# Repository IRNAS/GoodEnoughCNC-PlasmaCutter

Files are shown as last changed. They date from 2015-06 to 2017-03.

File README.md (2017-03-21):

# GoodEnoughCNC-Hybrid

#### ! PLEASE NOTE THAT WE NO LONGER ACTIVELY SUPPORT THIS PROJECT. 

**GoodEnoughCNC Hybrid - very low cost and simple, suitable for everyone. Can be mill, plasma or laser cutter.**

You can find out more on the project website - [goodenoughcnc.eu](http://goodenoughcnc.eu/). Step-by-step assembly instructions are available at [instructions.goodenoughcnc.eu](http://instructions.goodenoughcnc.eu/). 

**Technical files for the last, improved version are available in the folder [HybridCNC_v3](https://github.com/IRNAS/GoodEnoughCNC-PlasmaCutter/tree/master/HybridCNC_v3). Please note that these improvements are not included in the [HybridCNC assembly instructions](http://instructions.goodenoughcnc.eu/).**

Industry in vast majority aims to use highest precision and reliability machines, to be capable of producing even the most complicated parts designers come up with. We are flipping such approach on its head, trading precision of manufacturing tools for simplicity and low cost of their construction, to reduce the entry barrier for using them in any environment. 

GoodEnoughCNC-PlasmaCutter

## Prototype Specifications
Every machine can be tailored to size.
The GoodEnoughCNC Hybrid is a parametric bootstrap machine. Dimensions depend on the length of the profiles (Parameter L) and profile sizes. The specification below applies for L=1200mm profiles. 

### Frame Metric
 * 40 mm steel tubes
 * 3 mm thickness

### Trolleys Metric
 * 100 mm steel tubes
 * 3 mm thicknes

### Footprint
 * Width: 1450 mm 
 * Length: 900 mm

### Cutting area
 * Width: L-900 mm
 * Length: L-900 mm

### Z travel
 * Height: Z axis rod length - 150 mm

### XY Motion system
 * Timing belt and pulley (T5 or HTD5M or HTD3M or GT2[worst case])
 * Nema 23 motors

### Z Motion system
 * Threaded rod
 * Nema 17 motor

### Plasma
 * Low cost hand held plasma (BMF CUT 50M) or similar
 * THC (Torch height controller)
 * Compressor 30-100 l/min at 2-4 bar – effective 180 l/min

###CNC Controller
Any 4 channel CNC controller, tested:
 * Planet CNC MK3/4 USB Controller
 * Stepper drivers 2.5 A
 * 24 or 48 VDC Power supply

## Features

### Simplicity
Can be manufactured using a hand held drill and angle grinder. Non critical parts are 3D and can be made using other manufacturing processes

### Frame
Low cost Square tubes are used as structural components and linear rails for trolleys. The frame is kept in rectangular position using two turnbuckles. Removing the turnbuckles allows folding the frame for easy transport. 

GoodEnoughCNC-PlasmaCutter

GoodEnoughCNC-PlasmaCutter

### Trolleys
Low cost square tubes with holes for motor, bearing positions and tightening. Tightening mechanisms compensate for loose tolerances in hole positioning. The result is a exact fit on the frame.

GoodEnoughCNC-PlasmaCutter

GoodEnoughCNC-PlasmaCutter

### Z Axis
Lighter and simpler to manufacture, the Z axis mechanism does not require milled parts like conventional solutions. The torch holder tightly locks the torch in place without having to modify the handle.

GoodEnoughCNC-PlasmaCutter

### Plasma
The Chinese BMF CUT 50M plasma cutter packs more than enough punch to cleanly cut up to 5 mm sheet metal (10 mm max cut). Additionally a compressor and torch height controller is needed.

GoodEnoughCNC-PlasmaCutter

## Control system
A number of different CNC controller systems may be applied to this machine. Additionally we have developed an unique fibre optics based interface for the plasma cutter itself, reducing the cost of adding a Torch Height Controller with our custom design, enabling cutting of warped or corrugated surfaces.

### Configuration for CNC control systems
 * Steps per unit X, Y (steps/mm): 67.67 (using 1/16 microstepping by default)
 * Steps per unit Z (steps/mm): 2560 (using 1/16 microstepping by default)
 * Maximum speed X, Y(mm/min): 8000
 * Maximum speed Z (mm/min): 250
 * Acceleration X,Y (mm^2/min): 80
 * Acceleration Z (mm^2/min): 25
 
Setting file for PlanetCNC is [available](goodenoughcnc-hybrid-planetcnc.setting).

### Configuring Goodrive10 VFD inverter for 0.8kW watercooled spindle
Manufacturers [user manual for Goodrive10](http://www.invt.com/UploadFiles/en/Files/2013/9/Goodrive10%20Operation%20Manual(V1.3).pdf) documents well all the features. Spindle specific settings for 0.8kW spindle are, modified from defaults:
 * P00.03 400
 * P00.04 400
 * P02.02 400
 
With this the spindle should run at 24000rpm, note the display either shows 24000 in rpm or 400 in Hz, both representing the same speed.

## Q&A

[Here](https://github.com/IRNAS/GoodEnoughCNC-PlasmaCutter/blob/master/Q%26A.md) you can read the answers to some frequently asked questions.

---

#### License

All our projects are as usefully open-source as possible.

Hardware including documentation is licensed under [CERN OHL v.1.2. license](http://www.ohwr.org/licenses/cern-ohl/v1.2)

Firmware and software originating from the project is licensed under [GNU GENERAL PUBLIC LICENSE v3](http://www.gnu.org/licenses/gpl-3.0.en.html).

Open data generated by our projects is licensed under [CC0](https://creativecommons.org/publicdomain/zero/1.0/legalcode).

All our websites and additional documentation are licensed under [Creative Commons Attribution-ShareAlike 4 .0 Unported License] (https://creativecommons.org/licenses/by-sa/4.0/legalcode).

What this means is that you can use hardware, firmware, software and documentation without paying a royalty and knowing that you'll be able to use your version forever. You are also free to make changes but if you share these changes then you have to do so on the same conditions that you enjoy.

Koruza, GoodEnoughCNC and IRNAS are all names and marks of Institut IRNAS Rače. 
You may use these names and terms only to attribute the appropriate entity as required by the Open Licences referred to above. You may not use them in any other way and in particular you may not use them to imply endorsement or authorization of any hardware that you design, make or sell.

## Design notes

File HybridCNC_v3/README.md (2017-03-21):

# HybridCNC Improvements

Here you can find documentation for several improvements to our GoodEnoughCNC Hybrid, which are simplifying the design and making the machine more robust. Everyone interested only in the changes compared to previous version can find the changed files in the folder [HybridCNC-Changed-files-only](https://github.com/IRNAS/GoodEnoughCNC-PlasmaCutter/tree/master/HybridCNC_v3/HybridCNC-Changed-files-only). Please note that these improvements are not included in the [HybridCNC assembly instructions](https://goodenoughcnc-hybrid-cnc.readme.io/docs). 

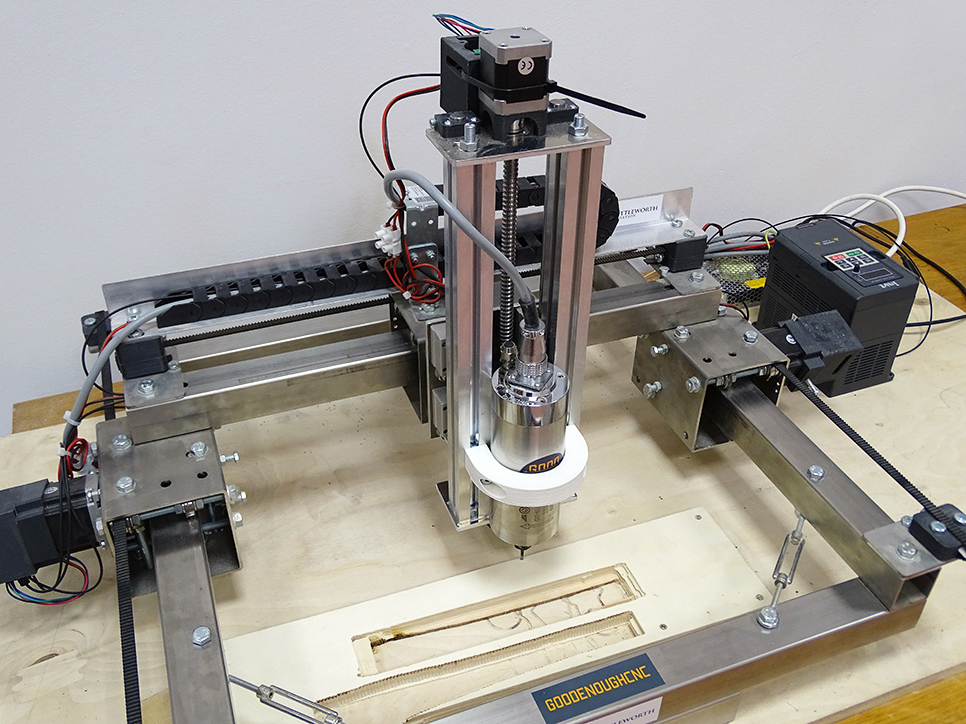
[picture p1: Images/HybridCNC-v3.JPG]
HybridCNC-v3


## Z axis

We completely changed the structure of the Z axis. Instead of the axial bearings used for railing system we decided to use a linear bearing with casings, which makes the axis sturdier and much more accurate. We replaced the M8 rod used for linear movement of the Z axis with a ball screw and an anti backlash nut with 4 mm pitch, further increasing the accuracy of the whole system, enabling finer movement and longer lifetime. The base plate is now made out of 5 mm aluminium plate, which also increases the structural strength. 

HybridCNC-z-axis

## Tightener

We made some minor changes to the tighteners, mostly reducing parts count and enabling easier installation. The tightener bracket is now a one piece laser cut part made out of tubular stainless steel profile. We also replaced the nuts with a screwing tightener with threads already implemented into the model.

HybridCNC-tightener

## Beam short for trolley assembly

We added inspection holes used in mounting process of the ball bearings, which help with accurate placement of the ball bearings.

HybridCNC-trolley

---

#### License

All our projects are as usefully open-source as possible.

Hardware including documentation is licensed under [CERN OHL v.1.2. license](http://www.ohwr.org/licenses/cern-ohl/v1.2)

Firmware and software originating from the project is licensed under [GNU GENERAL PUBLIC LICENSE v3](http://www.gnu.org/licenses/gpl-3.0.en.html).

Open data generated by our projects is licensed under [CC0](https://creativecommons.org/publicdomain/zero/1.0/legalcode).

All our websites and additional documentation are licensed under [Creative Commons Attribution-ShareAlike 4 .0 Unported License] (https://creativecommons.org/licenses/by-sa/4.0/legalcode).

What this means is that you can use hardware, firmware, software and documentation without paying a royalty and knowing that you'll be able to use your version forever. You are also free to make changes but if you share these changes then you have to do so on the same conditions that you enjoy.

Koruza, GoodEnoughCNC and IRNAS are all names and marks of Institut IRNAS Rače. 
You may use these names and terms only to attribute the appropriate entity as required by the Open Licences referred to above. You may not use them in any other way and in particular you may not use them to imply endorsement or authorization of any hardware that you design, make or sell.

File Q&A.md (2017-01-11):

#GoodEnoughCNC Q&A

Here you can read the answers to some frequently asked questions. Please get in touch via [chat](https://chat.irnas.eu/home), [forum](https://goodenoughcnc-hybrid-cnc.readme.io/discuss) or [email](mailto:info@irnas.eu) if you don't find what you're looking for below.

**1. What are the dimensions of GoodEnoughCNC?**

The default version of GoodeenoughCNC machine is 1.1 m x 1.1 m . We do not recommend exceeding the 2 m x 1.2 m dimensions for plasma operations. For milling it depends on your speed and precision requirements.

**2. Is the machining toolhead included in your GoodEnoughCNC kit?**

GoodEnoughCNC kit is the machine without the toolhead, you can mount a
number of different ones on it:

1) Mill : mechanical subtraction of material with a milling bit suitable for most materials ([0.8 kW watercooled spindle](http://fabrikor.eu/goodenoughcnc-hybrid/toolhead-milling-0.8-kw-spindle) available from our store).

2) Plasma: cutting metal with a conductive arc ([plasma cutting torch](http://fabrikor.eu/goodenoughcnc-hybrid/toolhead-plasma-cutting-41) available from our store).

3) Laser: cutting various materials, subject to laser power. We have no laser cutters in our offer at the moment.

**3. Can I cut or engrave MDF with the laser or plasma? The thickest MDF is 18 mm, can your laser cut it at thoroughly in single pass at that depth?**

MDF you can cut only with a mill, laser cutting it may produce hazardous vapors. You can buy a number of different milling bits for different applications. The spindle we offer uses ER11 collets, meaning it can fit bits with shaft ranging from 1-7 mm.

**4. Can I use my own plasma cutter with GoodEnoughCNC?**

To use any plasma cutter with GoodenoughCNC machine one must 3D print a suitable torch mount, modify the plasma cutter such that cutting can be triggered from the control circuit (for example with GoodenoughCNC optical relay, to be released shortly) and optionally connect a Torch Height Controller unit to the plasma torch.

**5. What software is required to work with GoodEnoughCNC?**

The design and G-code generation is best done with [Autodesk Fusion 360](http://www.autodesk.com/products/fusion-360/overview), free and powerful. You also generally require a PC to run CNC software, you can either choose [Planet-CNC controller](http://fabrikor.eu/goodenoughcnc-hybrid/planet-cnc-usb-controller-mk3-4-4axis) that will be bundled with next generation of GoodenoughCNC Hybrid or use any open-source solution, like Arduino+GRBL and control it with one of many applications that exist, but neither really works that great. [GRBL-panel](https://github.com/gerritv/Grbl-Panel/wiki) seems to be one of the more working ones.

**6. What are configuration settings for CNC Control system?**

A number of different CNC controller systems may be applied to this machine. Additionally we have developed an unique fibre optics based interface for the plasma cutter itself, reducing the cost of adding a Torch Height Controller with our custom design, enabling cutting of warped or corrugated surfaces.

Configuration for CNC control systems
- Steps per unit X, Y (steps/mm): 67.67 (using 1/16 microstepping by default)
- Steps per unit Z (steps/mm): 2560 (using 1/16 microstepping by default)
- Maximum speed X, Y(mm/min): 8000
- Maximum speed Z (mm/min): 250
- Acceleration X,Y (mm^2/min): 80
- Acceleration Z (mm^2/min): 25

Setting file for PlanetCNC is available [here](https://github.com/IRNAS/GoodEnoughCNC-PlasmaCutter/blob/master/goodenoughcnc-hybrid-planetcnc.setting).

**7. We cannot configure the inverter for spindle. Do you have a manual or something so that we can change the rpm of the spindle?**

Configuring Goodrive10 VFD inverter for 0.8 kW watercooled spindle:

[Manufacturers user manual](www.invt.com/UploadFiles/en/Files/2013/9/Goodrive10%20Operation%20Manual(V1.3).pdf) for Goodrive10 documents well all the features. Spindle specific settings for 0.8kW spindle are, modified from defaults:
- P00.03 400
- P00.04 400
- P02.02 400

With this the spindle should run at 24000 rpm, note the display either shows 24000 in rpm or 400 in Hz, both representing the same speed.

**8. The collet falls from the spindle after some time. What can I do?**

Collet falls from spindle if it is rotating anti-clockwise, please check the rotation direction. You can change the direction by swapping the U and W wires on VFD.

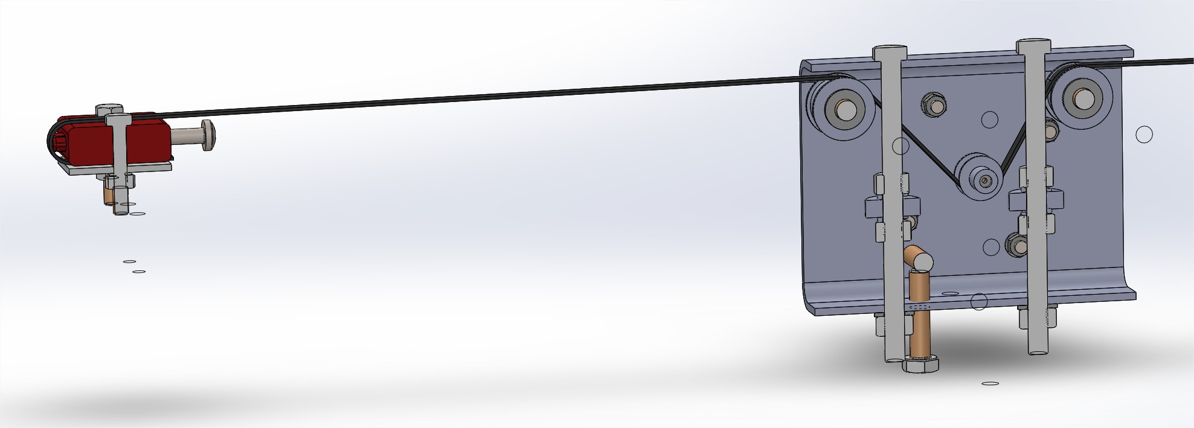
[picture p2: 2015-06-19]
Images/Trolley_inside.jpg

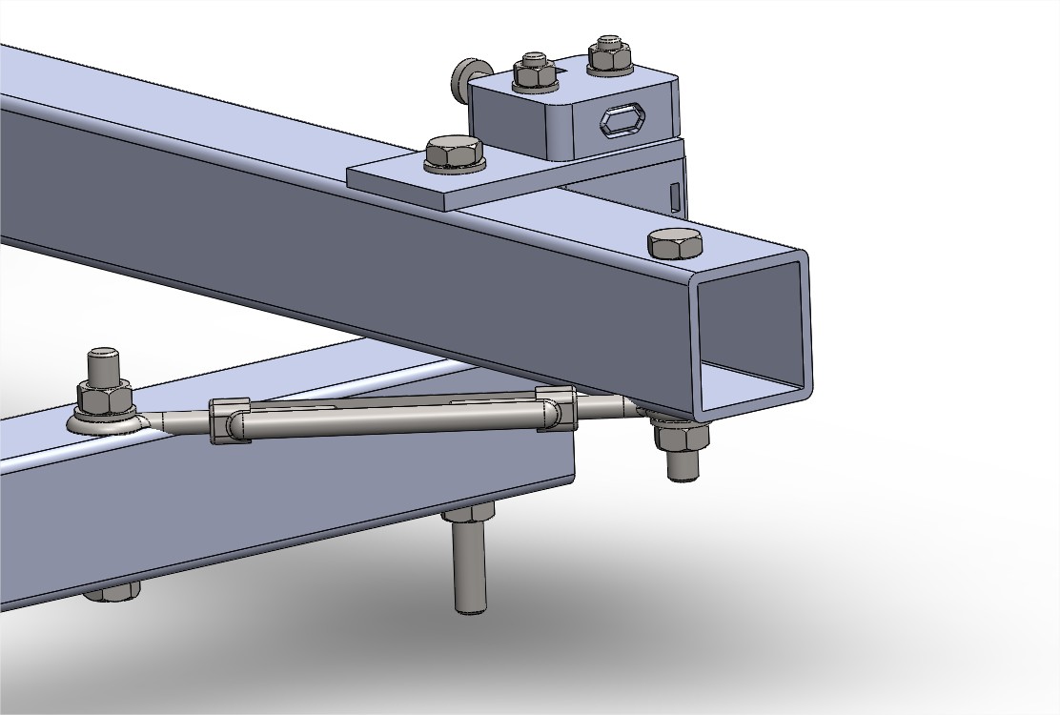
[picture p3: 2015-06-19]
Images/Turnbuckles.jpg

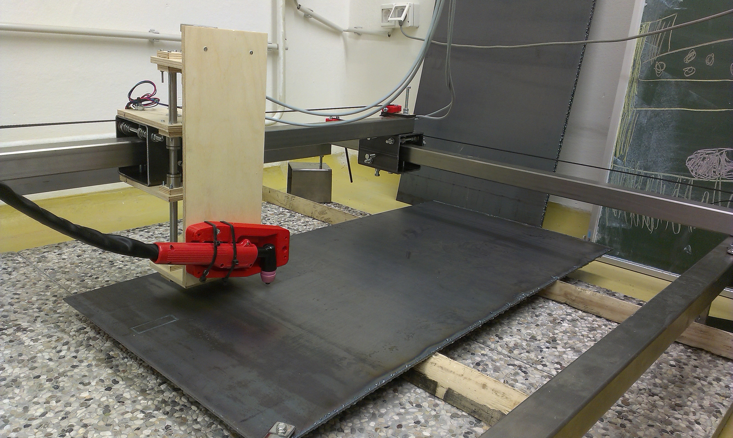
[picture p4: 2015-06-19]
Images/CNC_Plasma.jpg

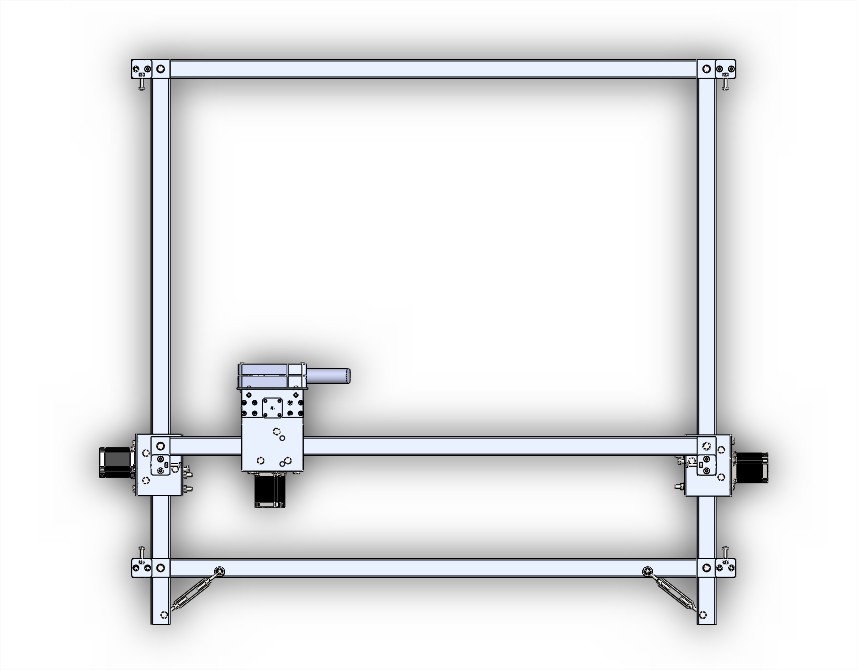
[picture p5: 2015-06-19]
Images/Frame_Top_View.jpg

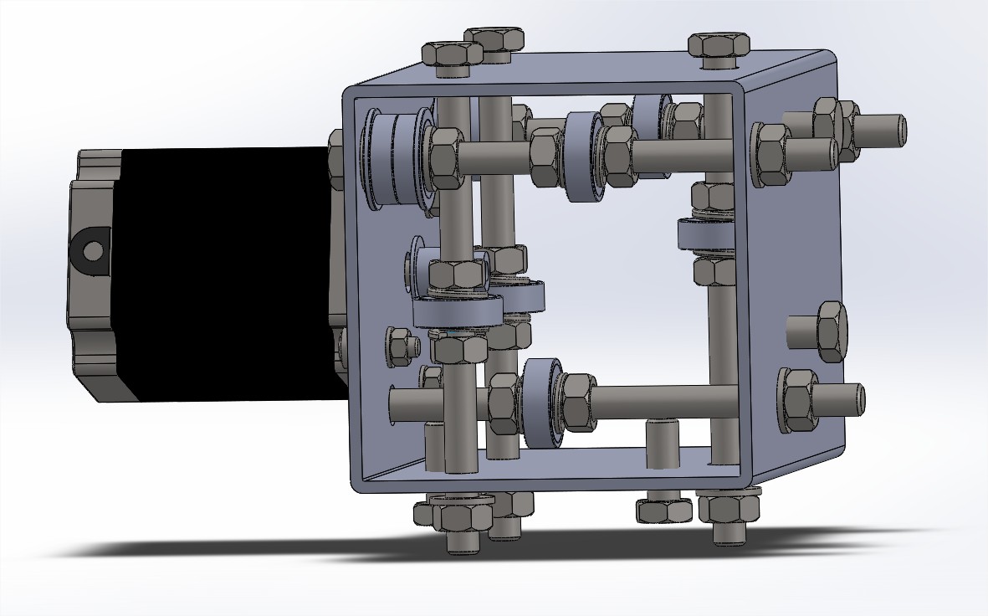
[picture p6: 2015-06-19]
Images/Trolley.jpg

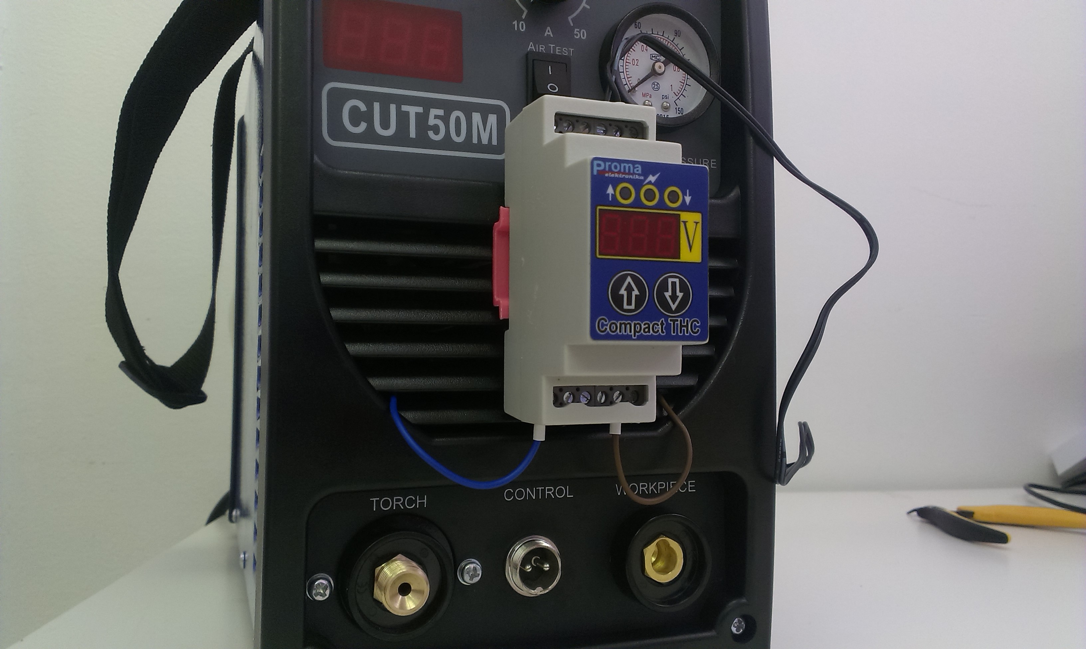
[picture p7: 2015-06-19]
Images/Plasma_and_Height_controller.jpg

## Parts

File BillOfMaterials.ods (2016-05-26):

STEEL BEAMS, PLATES
ITEM NO. | PART | DESCRIPTION | QTY.
1 | Beam X1 | SHS 40x40x3x1200 | 1
2 | Beam X2 | SHS 40x40x3x1200 | 1
3 | Beam X - Main | SHS 40x40x3x1200 | 1
4 | Beam Y | SHS 40x40x3x1200 | 2
5 | L Profile - Chain Support | L Profile 40x40x3x1200 | 1
6 | Beam Short X | SHS 100x100x3x130 | 1
7 | Beam Short Y1 | SHS 100x100x3x130 | 1
8 | Beam Short Y2 | SHS 100x100x3x130 | 1
9 | Aluminum profile | X Profile 30x30x300 | 2
10 | Bearing plate | 5mm Plate | 1
11 | Motor plate | 5mm Plate | 1
12 | Bottom plate | 5mm Plate | 1
13 | Bracket for tighteners - left |  | 3
14 | Bracket for tighteners - right |  | 3
15 | L Bracket - Chain Support | L Bracket 80x80 | 2
BOLTS, NUTS, WASHERS
ITEM NO. | PART | DESCRIPTION | QTY.
1 | DIN 933 M8x140 | M8 Hex Bolt | 2
2 | DIN 933 M8x120 | M8 Hex Bolt | 22
3 | DIN 933 M8x60 | M8 Hex Bolt | 6
4 | DIN 933 M8x55 | M8 Hex Bolt | 2
5 | DIN 933 M8x50 | M8 Hex Bolt | 8
6 | DIN 933 M8x25 | M8 Hex Bolt | 4
7 | DIN 933 M8x20 | M8 Hex Bolt | 16
8 | DIN 7985 M6x50 | M6 Cross Bolt | 4
9 | DIN 7985 M6x25 | M6 Cross Bolt | 15
10 | DIN 7985 M5x25 | M5 Cross Bolt | 12
11 | DIN 912 M4x16 | M4 Hex Socket Bolt | 4
12 | DIN 912 M3x35 | M3 Hex Socket Bolt | 1
13 | DIN 912 M3x16 | M3 Hex Socket Bolt | 1
14 | ISO 14583 M3x12 | M3 Torx Bolt | 12
15 | DIN 7996 4.5x50 | Wood Cross Screw | 4
16 | DIN 934 M8 8.8 | M8 Hex Nut | 101
17 | DIN 934 M6 8.8 | M6 Hex Nut | 15
18 | DIN 934 M5 8.8 | M5 Hex Nut | 36
19 | DIN 934 M3 8.8 | M3 Hex Nut | 13
20 | DIN 934 M4 8.8 | M4 Hex Nut | 4
21 | DIN 562 M8 | M8 Square Nut | 6
22 | DIN 562 M3 | M3 Square Nut | 1
23 | DIN 125 8.4 | M8 Washer | 72
24 | DIN 125 6.4 | M6 Washer | 12
25 | DIN 125 5.3 | M5 Washer | 16
26 | DIN 125 3.2 | M3 Washer | 4
27 | DIN 127 8.5 | M8 Spring Washer | 36
3D PRINTED PARTS
ITEM NO. | PART | DESCRIPTION | QTY.
1 | Tightener - Outer | Tightener – Outer.STL | 6
2 | Tightener - Spacer | Tightener – Spacer.STL | 2
3 | Linear guide mount | Linear guide mount.STL | 4
4 | Nut casing - Upper | Nut casing – Upper.STL | 1
5 | Nut casing - Bottom | Nut casing – Bottom.STL | 1
6 | Torch mount | Torch mount.STL | 1
OTHER
ITEM NO. | PART | DESCRIPTION | QTY.
1 | Bearing 608ZZ | Ball Bearing outer diam. 22 | 18
2 | Bearing F608Z | Belt Ball Bearing outer diam. 22 | 12
3 | Flanged Timing Pulley | 16 teeth HTD3M/16 or DIN 7721 T5/16 | 3
4 | Micro switch | Micro End Switch | 4
5 | NEMA 17 Stepper Motor |  | 1
6 | NEMA 23 Stepper motor |  | 3
7 | Linear guide fi12x270 | Round Rod | 2
8 | Rod M8x200 | M8 Rod | 1
9 | Coupler 5 to 8 mm | Flexible shaft coupler | 1
10 | Turnbuckle M6 | M6 2x Eye70 mm | 2
11 | Screw Anchor fi10 | Plasterboard Anchor | 4
12 | Timing Belt | HTD3M or T5, width 10, length 1400 | 3
13 | Cable Chain | length 1400, inner size 25x15, radius 50 | 1

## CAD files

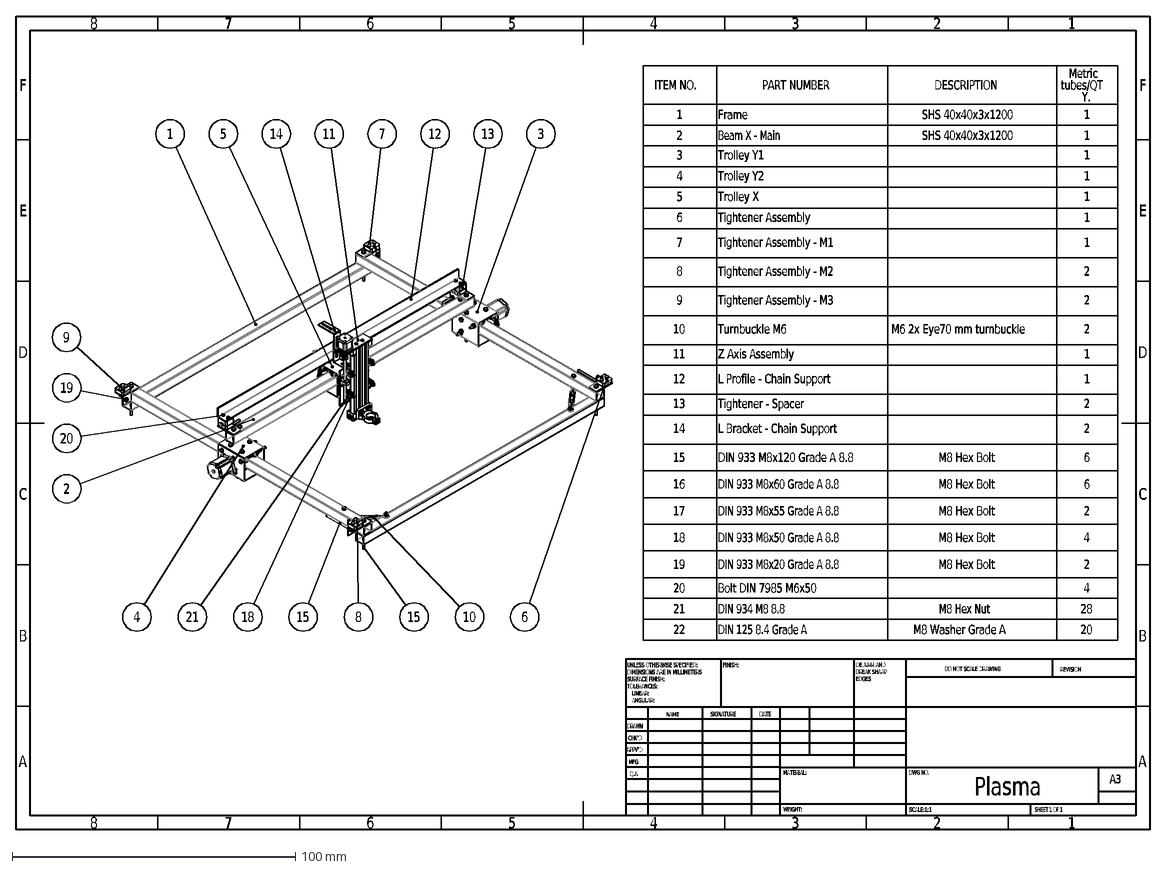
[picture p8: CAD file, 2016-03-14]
Drawings/Plasma.DXF
A
B
C
D
E
F
8
7
6
5
4
3
2
1
DRAWN
CHK'D
APPV'D
MFG
Q.A
UNLESS OTHERWISE SPECIFIED:
DIMENSIONS ARE IN MILLIMETERS
SURFACE FINISH:
TOLERANCES:
LINEAR:
ANGULAR:
FINISH:
DEBURR AND
BREAK SHARP
EDGES
NAME
SIGNATURE
DATE
MATERIAL:
DO NOT SCALE DRAWING
REVISION
DWG NO.
SCALE:1:1
SHEET 1 OF 1
A3
WEIGHT:
Plasma
ITEM NO.
PART NUMBER
DESCRIPTION
Metric
tubes/QT
Y.
Frame
SHS 40x40x3x1200
Beam X - Main
Trolley Y1
Trolley Y2
Trolley X
Tightener Assembly
Tightener Assembly - M1
Tightener Assembly - M2
9
Tightener Assembly - M3
10
Turnbuckle M6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

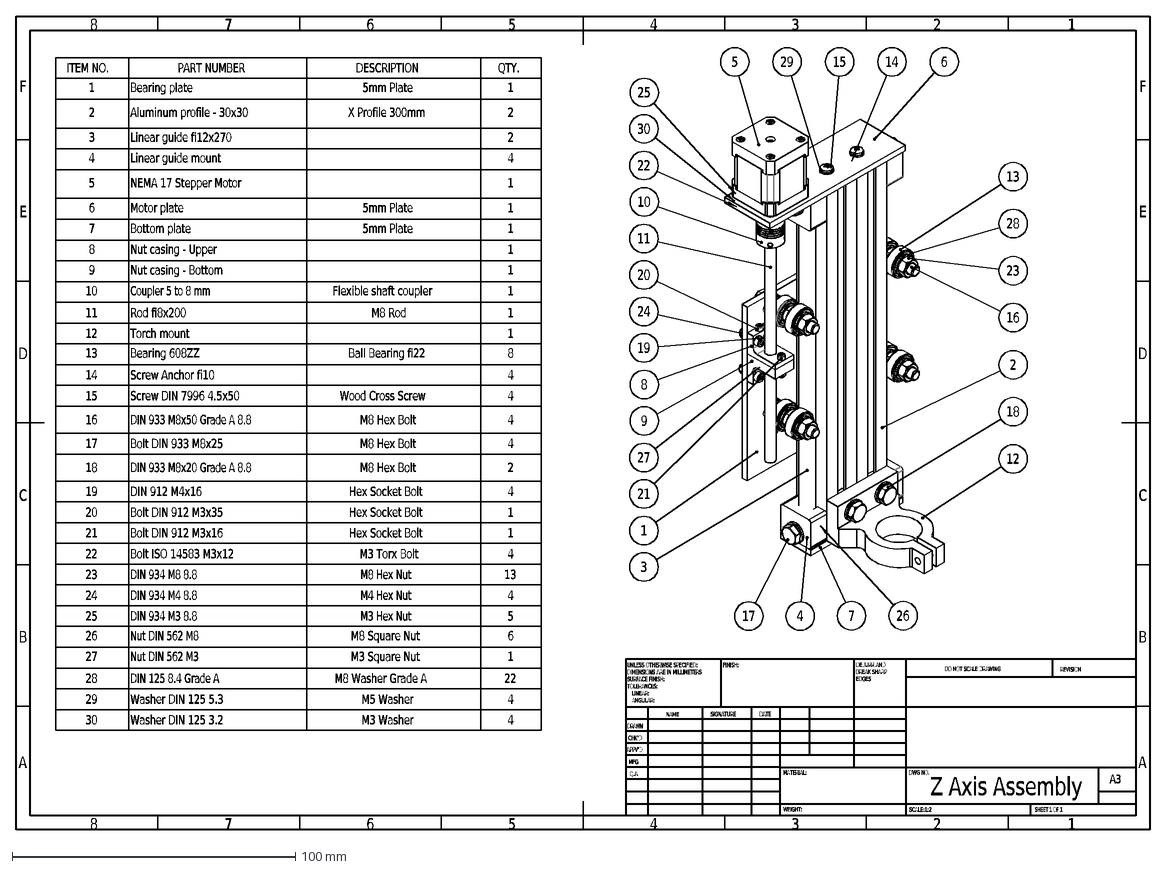
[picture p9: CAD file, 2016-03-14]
Drawings/Z Axis Assembly/DXF/Z Axis Assembly.DXF
DRAWN
CHK'D
APPV'D
MFG
Q.A
UNLESS OTHERWISE SPECIFIED:
DIMENSIONS ARE IN MILLIMETERS
SURFACE FINISH:
TOLERANCES:
LINEAR:
ANGULAR:
FINISH:
DEBURR AND
BREAK SHARP
EDGES
NAME
SIGNATURE
DATE
MATERIAL:
DO NOT SCALE DRAWING
REVISION
DWG NO.
SCALE:1:2
SHEET 1 OF 1
A3
WEIGHT:
Z Axis Assembly
A
B
C
D
E
F
8
7
6
5
4
3
2
1
ITEM NO.
PART NUMBER
DESCRIPTION
QTY.
Bearing plate
5mm Plate
Aluminum profile - 30x30
X Profile 300mm
Linear guide fi12x270
Linear guide mount
NEMA 17 Stepper Motor
Motor plate
Bottom plate
Nut casing - Upper
9
Nut casing - Bottom
10
Coupler 5 to 8 mm
Flexible shaft coupler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

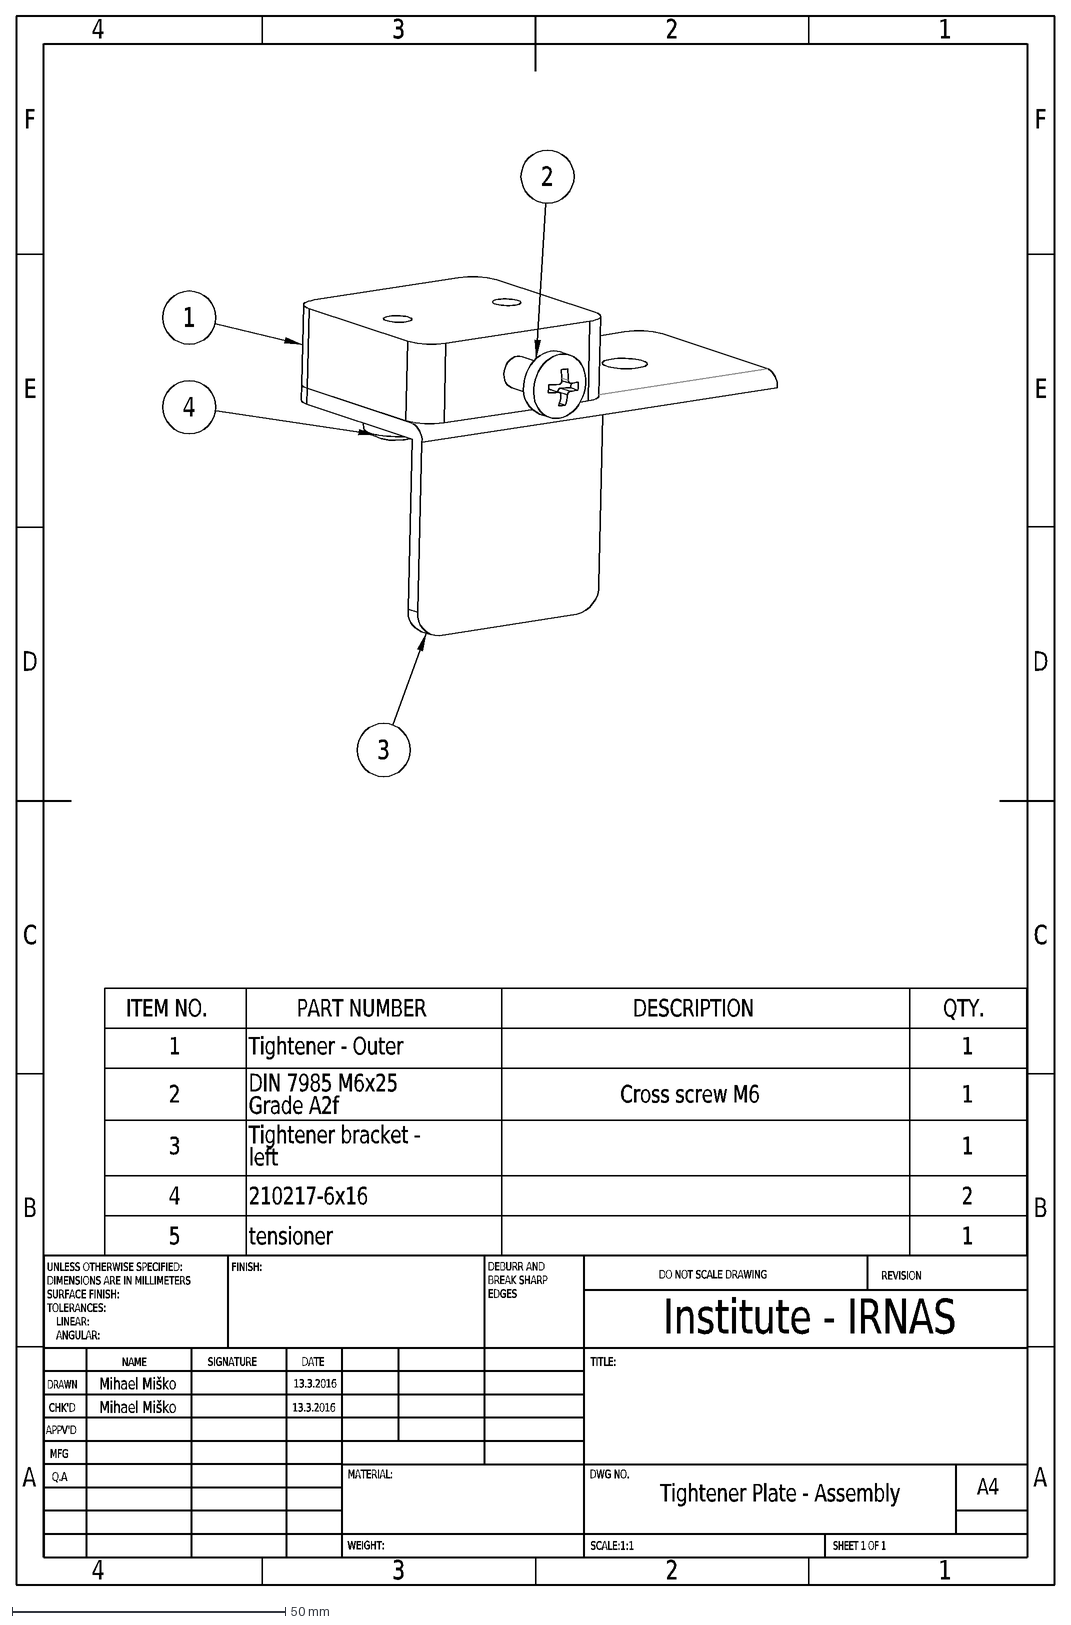
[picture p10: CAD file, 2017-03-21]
HybridCNC_v3/HybridCNC - Drawings/DXF drawings/Tightener Plate - Assembly.DXF
C
D
E
B
F
A
2
3
1
4
DRAWN
CHK'D
APPV'D
MFG
Q.A
UNLESS OTHERWISE SPECIFIED:
DIMENSIONS ARE IN MILLIMETERS
SURFACE FINISH:
TOLERANCES:
LINEAR:
ANGULAR:
FINISH:
DEBURR AND
BREAK SHARP
EDGES
NAME
SIGNATURE
DATE
MATERIAL:
DO NOT SCALE DRAWING
REVISION
TITLE:
DWG NO.
SCALE:1:1
SHEET 1 OF 1
A4
Mihael Miško
13.3.2016
Tightener Plate - Assembly
Institute - IRNAS
WEIGHT:
ITEM NO.
PART NUMBER
DESCRIPTION
QTY.
Tightener - Outer
DIN 7985 M6x25
Grade A2f
Cross screw M6
Tightener bracket -
left
210217-6x16
5
tensioner

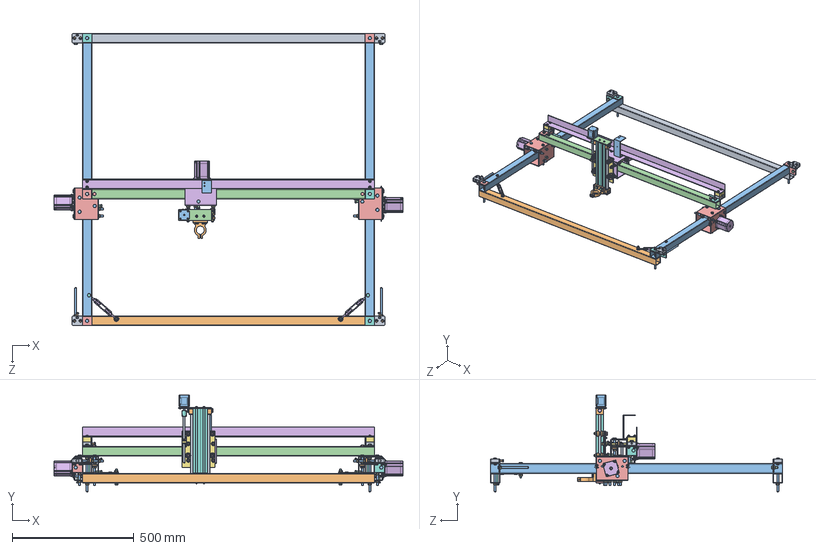
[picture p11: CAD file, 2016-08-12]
SolidWorks_Files/Plasma Beta.SLDASM
1432.0 x 396.6 x 1200.0 mm
Beam X1
Beam X2
Beam Y x 2
Beam X - Main
Beam Short Y1
NEMA 23 Stepper motor x 3
Timing pulley x 3
Micro switch x 4
Bearing F608Z x 12
Bearing 608ZZ x 26
DIN 933 M8x120 Grade A 8.8 x 22
DIN 933 M8x20 Grade A 8.8 x 16
DIN 7985 M5x25 Grade A2f x 12
Bolt ISO 14583 M3x12 x 12
DIN 934 M8 8.8 x 101
DIN 934 M5 8.8 x 36
DIN 934 M3 8.8 x 13
DIN 125 8.4 Grade A x 72
Washer DIN 125 5.3 x 16
DIN 127 8.5 x 36
Beam Short Y2
Beam Short X
DIN 933 M8x140 Grade A 8.8 x 2
Bracket for tighteners - left x 3
Tightener - Outer x 6
DIN 7985 M6x25 Grade A2f x 15
DIN 934 M6 8.8 x 15
DIN 125 6.4 Grade A x 12
Bracket for tighteners - right x 3
Turnbuckle M6 x 2
Bearing plate
Aluminum profile - 30x30 x 2
Linear guide fi12x270 x 2
Linear guide mount x 4
NEMA 17 Stepper Motor
Motor plate
Bottom plate
Nut casing - Upper
Nut casing - Bottom
Coupler 5 to 8 mm
Rod M8x200
Torch mount
Screw Anchor fi10 x 4
Screw DIN 7996 4.5x50 x 4
DIN 933 M8x50 Grade A 8.8 x 8
Bolt DIN 933 M8x25 x 4
DIN 912 M4x16 x 4
Bolt DIN 912 M3x35
Bolt DIN 912 M3x16
DIN 934 M4 8.8 x 4
Nut DIN 562 M8 x 6
Nut DIN 562 M3
Washer DIN 125 3.2 x 4
L Profile - Chain Support
Tightener - Spacer x 2
DIN 933 M8x60 Grade A 8.8 x 6
DIN 933 M8x55 Grade A 8.8 x 2
Bolt DIN 7985 M6x50 x 4
U Profile - Chain Support

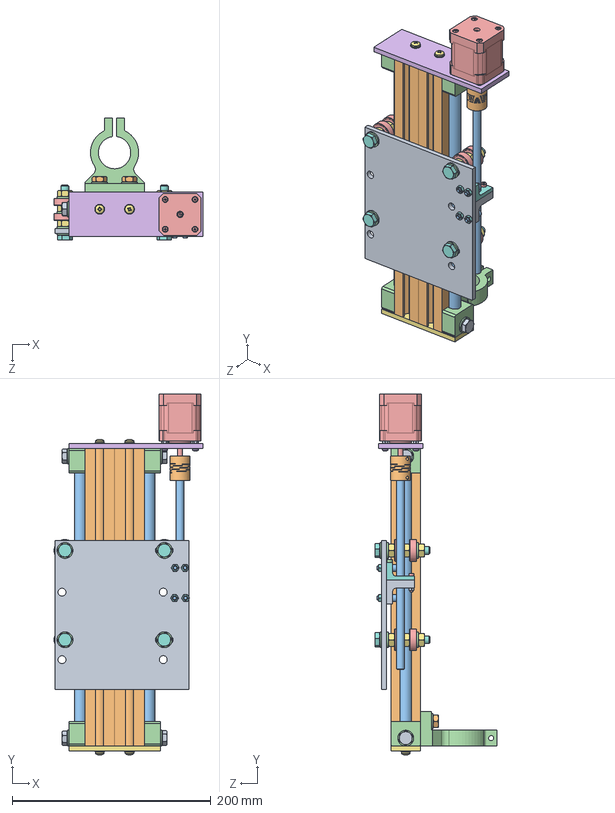
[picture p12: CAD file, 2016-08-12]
SolidWorks_Files/Z Axis Assembly.sldasm
150.0 x 363.7 x 123.1 mm
Bearing plate
Aluminum profile - 30x30 x 2
Linear guide fi12x270 x 2
Linear guide mount x 4
NEMA 17 Stepper Motor
Motor plate
Bottom plate
Nut casing - Upper
Nut casing - Bottom
Coupler 5 to 8 mm
Rod M8x200
Torch mount
Bearing 608ZZ x 8
Screw Anchor fi10 x 4
Screw DIN 7996 4.5x50 x 4
DIN 933 M8x50 Grade A 8.8 x 4
Bolt DIN 933 M8x25 x 4
DIN 933 M8x20 Grade A 8.8 x 2
DIN 912 M4x16 x 4
Bolt DIN 912 M3x35
Bolt DIN 912 M3x16
Bolt ISO 14583 M3x12 x 4
DIN 934 M8 8.8 x 13
DIN 934 M4 8.8 x 4
DIN 934 M3 8.8 x 5
Nut DIN 562 M8 x 6
Nut DIN 562 M3
DIN 125 8.4 Grade A x 22
Washer DIN 125 5.3 x 4
Washer DIN 125 3.2 x 4

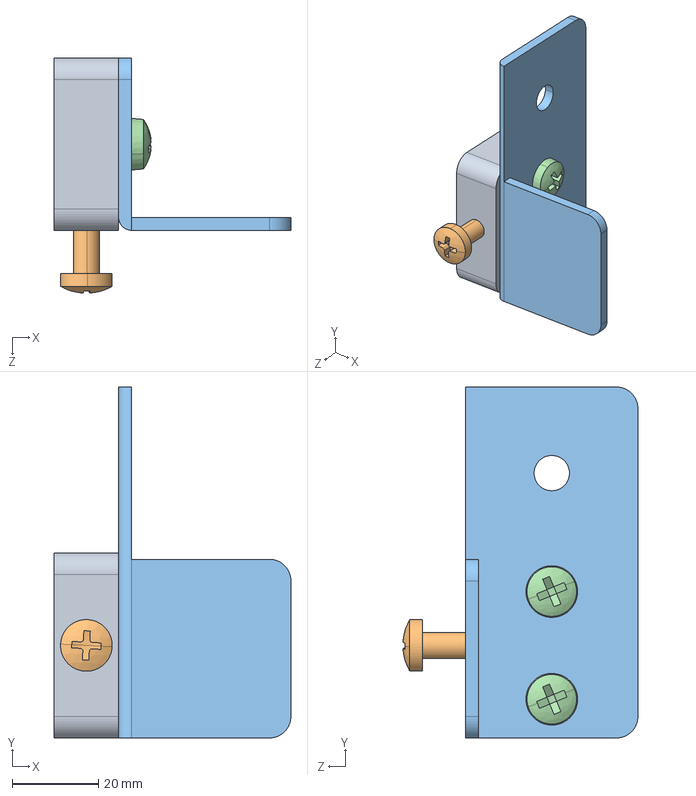
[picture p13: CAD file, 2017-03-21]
HybridCNC_v3/HybridCNC - 3D model/STEP Files/Tightener Plate - Assembly.STEP
55.0 x 81.5 x 54.5 mm
Tightener - Outer
DIN 7985 M6x25 Grade A2f
Tightener bracket - left
210217-6x16 x 2
tensioner

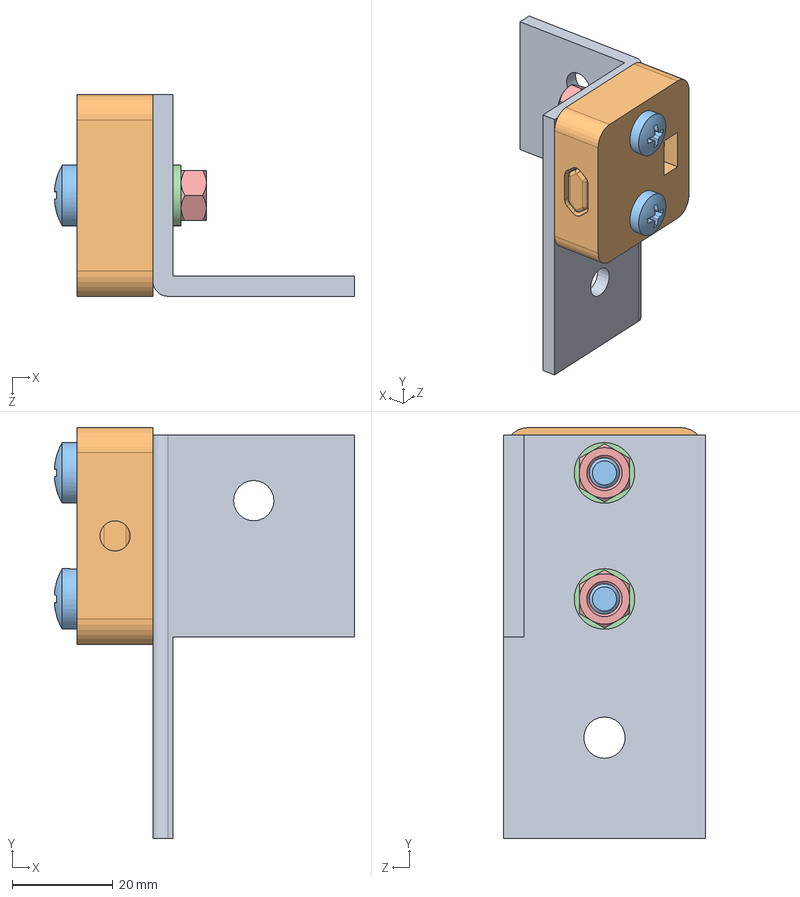
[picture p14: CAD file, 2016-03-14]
SolidWorks_Files/Tightener Assembly - M1.SLDASM
59.5 x 81.5 x 40.0 mm
Bracket for tighteners - right
Tightener - Outer
DIN 7985 M6x25 Grade A2f x 2
DIN 125 6.4 Grade A x 2
DIN 934 M6 8.8 x 2

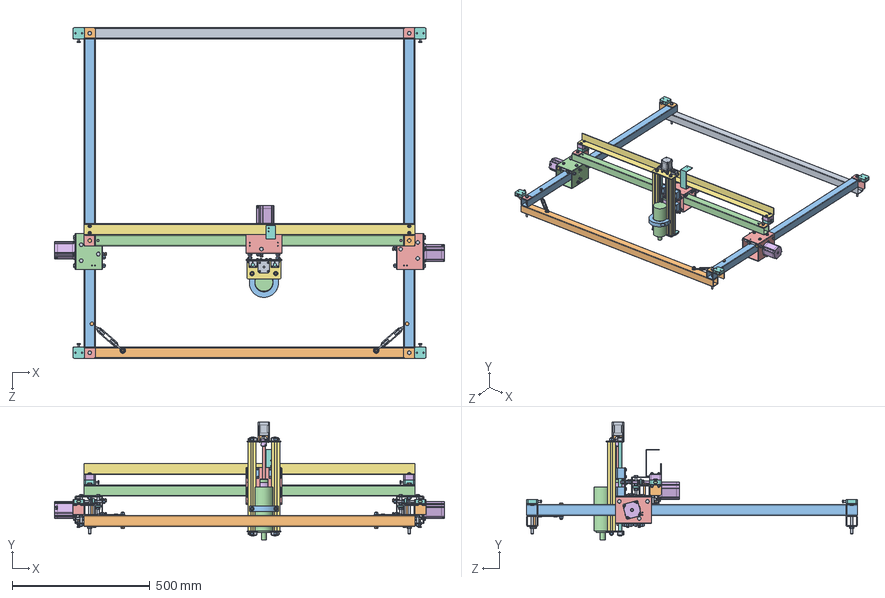
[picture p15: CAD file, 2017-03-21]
HybridCNC_v3/HybridCNC - 3D model/Plasma Beta.SLDASM
1416.0 x 426.8 x 1200.0 mm
Beam X1
Beam X2
Beam Y x 2
Beam X - Main
Beam Short Y1
NEMA 23 Stepper motor x 3
Bearing F608Z x 12
Bearing 608ZZ x 18
DIN 933 M8x110 Grade A 8.8 x 20
DIN 933 M6x20 Grade A 8.8 x 6
DIN 934 M8 8.8 x 84
DIN 934 M5 8.8 x 12
DIN 125 8.4 Grade A x 52
Washer DIN 125 5.3 x 12
DIN 127 8.5 x 36
Timing pulley - short x 3
210217-5x16 x 12
DIN 933 M6x25 Grade A 8.8 x 6
DIN 934 M6 8.8 x 32
Beam Short Y2
Beam Short X
DIN 933 M8x140 Grade A 8.8 x 2
DIN 933 M8x40 Grade A 8.8 x 2
Tightener - Outer x 6
DIN 7985 M6x25 Grade A2f x 6
Tightener bracket - left x 3
210217-6x16 x 8
tensioner x 6
Tightener bracket - right x 3
Tightener - Spacer x 2
L Profile - Chain Support
U Profile - Chain Support
Turnbuckle M6 x 2
DIN 933 M8x55 Grade A 8.8 x 6
Bolt DIN 7985 M6x50 x 4
ball screw nut SFU1204 fi12xfi22x40
ball screw SFU1204 fi12x300
coupler 5x8
profile aluminum 30x30x279 x 2
smooth rod fi12x314 x 2
stepper motor NEMA 17
threaded rod M8x310 x 2
Casing tipe SCE x 4
spindle
Base plate
nut mount
motor plate
Bottom plate
rod fixer x 4
adapter motor
spindle mount
Torx_screw_m3-30 x 8
Torx_screw_ m5-12 x 16
Torx_screw_m4-10 x 4
Torx_screw_m3-16 x 8
Torx_screw_m4-16 x 6
nut_din_557-m8_m_6_5 x 2
Guma
screw_iso_4762-m8x35-8_8 x 2

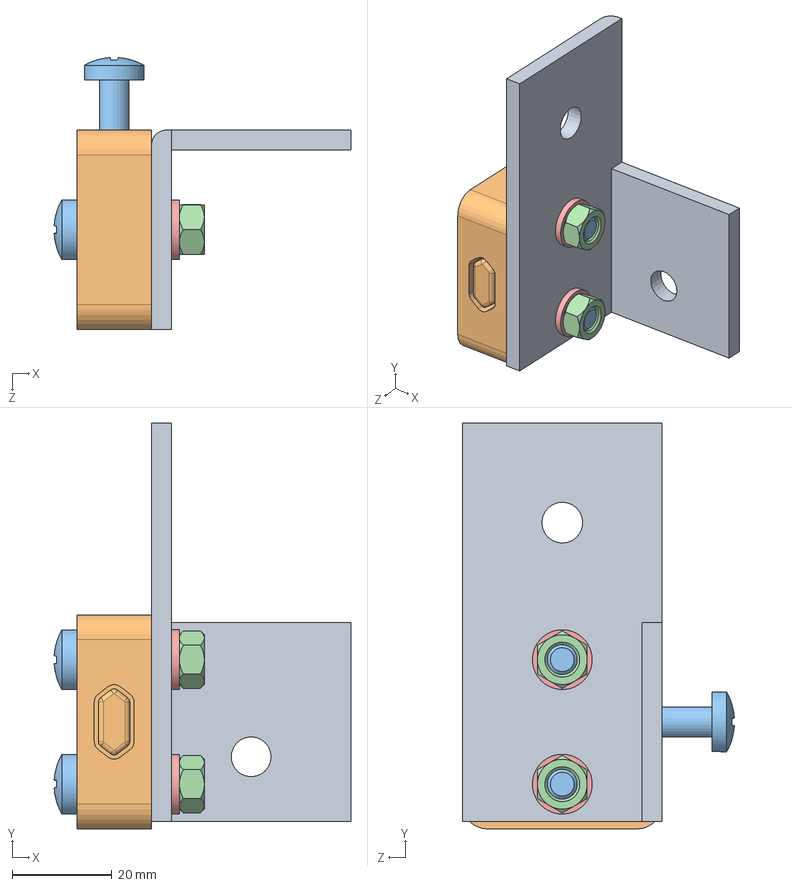
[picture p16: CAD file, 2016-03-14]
SolidWorks_Files/Tightener Assembly - M2.SLDASM
59.5 x 81.5 x 54.5 mm
Bracket for tighteners - right
Tightener - Outer
DIN 7985 M6x25 Grade A2f x 3
DIN 934 M6 8.8 x 3
DIN 125 6.4 Grade A x 2

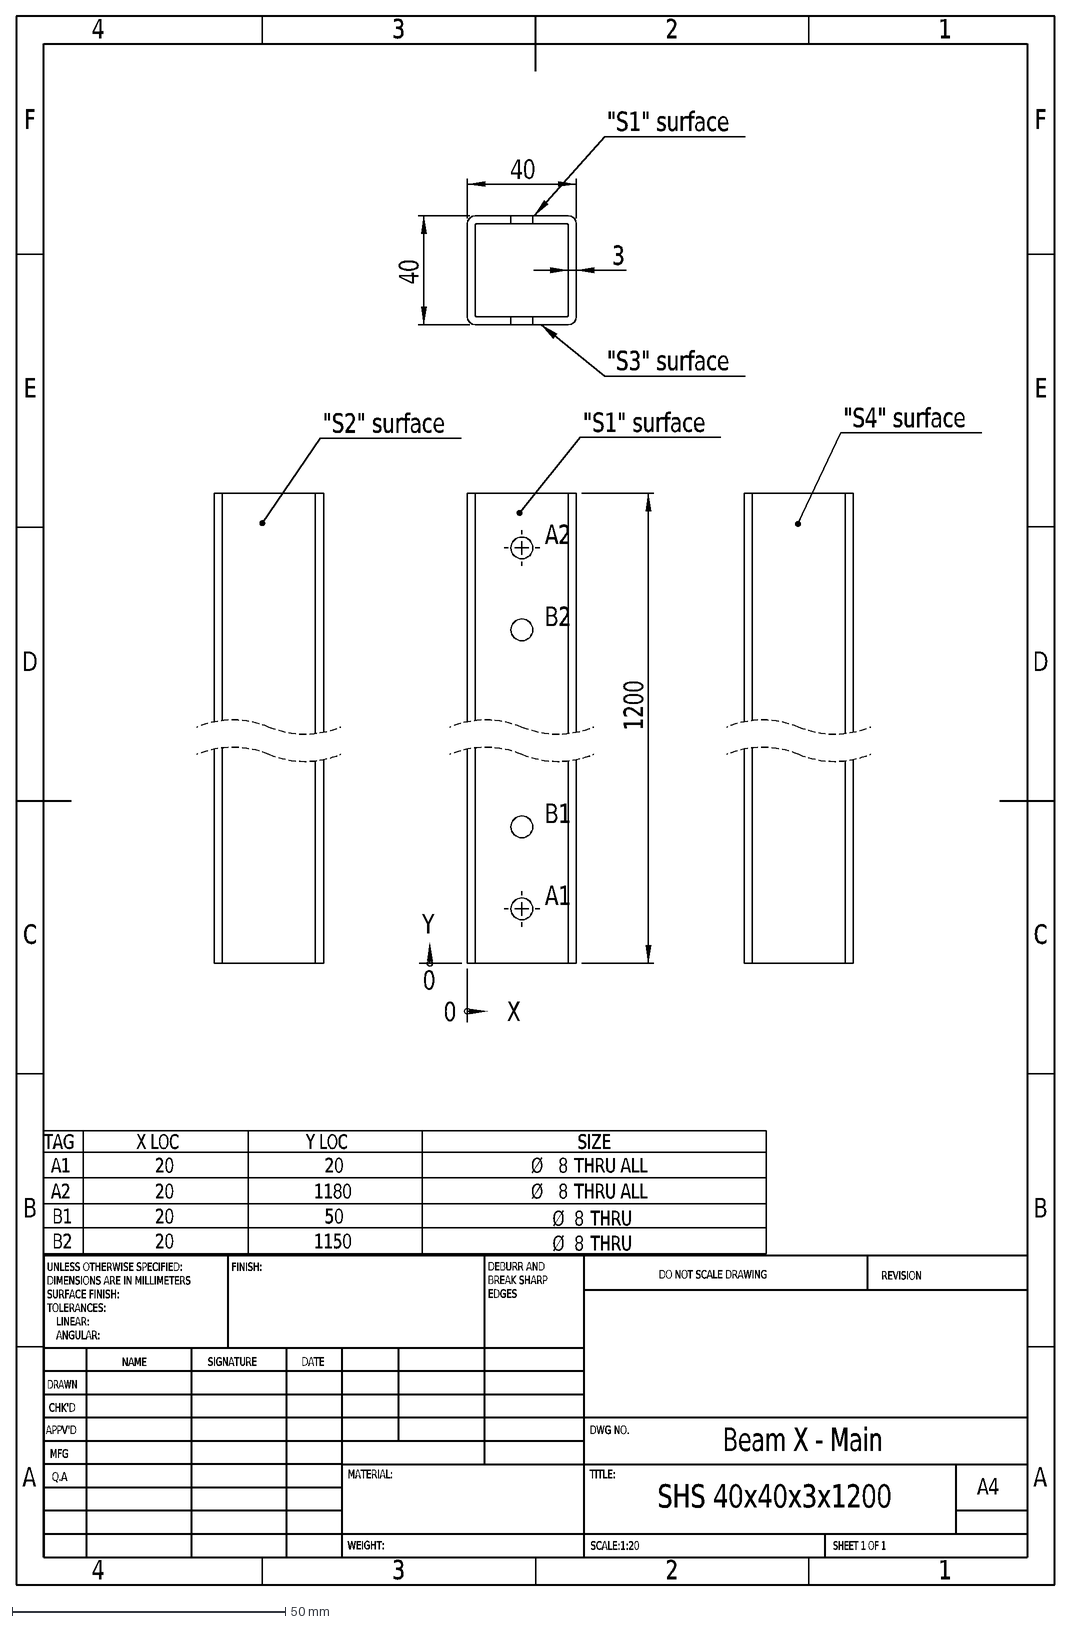
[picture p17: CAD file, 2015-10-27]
Drawings/Frame/DXF/Beam X - Main.DXF
C
D
E
B
F
A
2
3
1
4
DRAWN
CHK'D
APPV'D
MFG
Q.A
UNLESS OTHERWISE SPECIFIED:
DIMENSIONS ARE IN MILLIMETERS
SURFACE FINISH:
TOLERANCES:
LINEAR:
ANGULAR:
FINISH:
DEBURR AND
BREAK SHARP
EDGES
NAME
SIGNATURE
DATE
MATERIAL:
DO NOT SCALE DRAWING
REVISION
TITLE:
DWG NO.
SCALE:1:20
SHEET 1 OF 1
A4
WEIGHT:
Beam X - Main
SHS 40x40x3x1200
TAG
X LOC
Y LOC
SIZE
A1
20
Ø
8
THRU ALL
A2
1180
B1
50
THRU
B2
1150
1200
"S1" surface
X
Y
0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

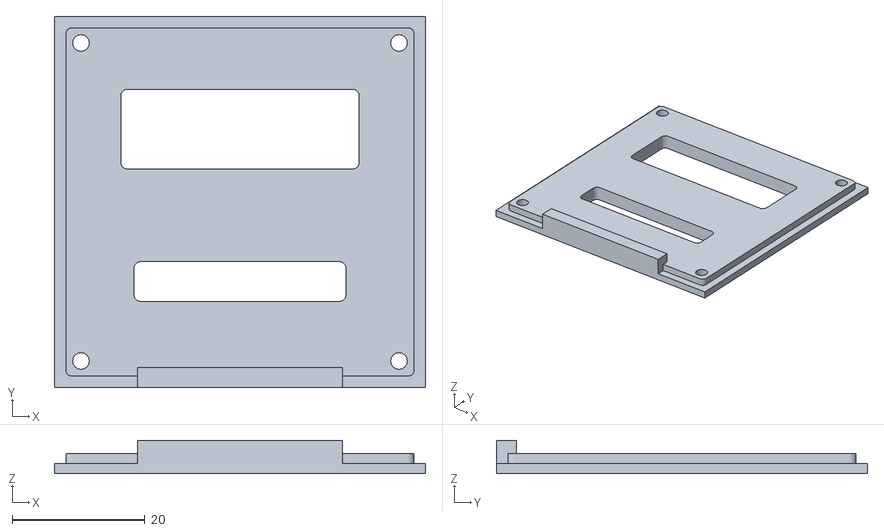
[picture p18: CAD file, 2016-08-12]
STL/Electronic Box Cover - Plasma - 4 piece(s).STL
56.0 x 56.0 x 5.00

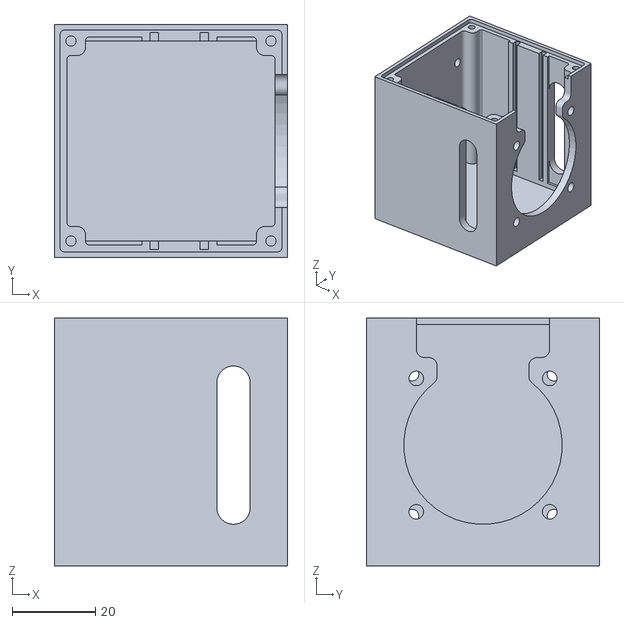
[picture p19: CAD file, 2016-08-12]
STL/Electronic Box - Plasma - 4 piece(s).STL
56.0 x 56.0 x 59.5

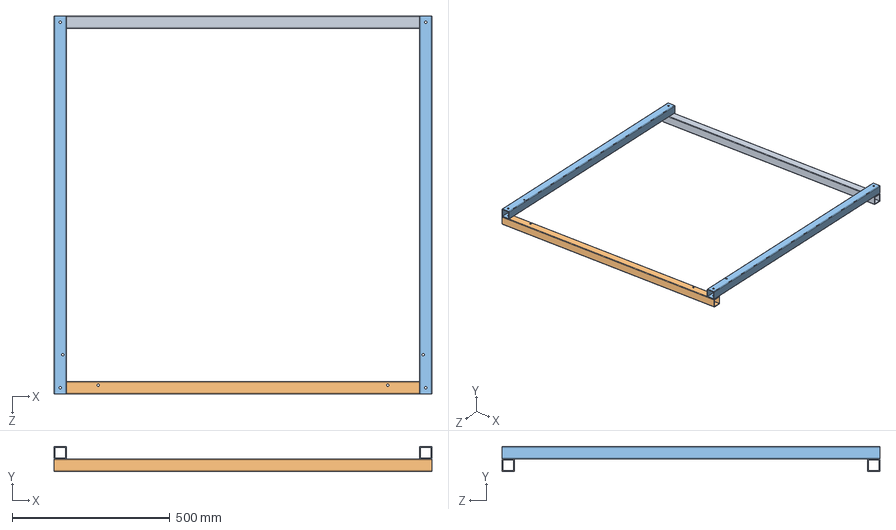
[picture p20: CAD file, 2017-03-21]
HybridCNC_v3/HybridCNC - 3D model/Frame.SLDASM
1200.0 x 80.0 x 1200.0 mm
Beam X1
Beam X2
Beam Y x 2

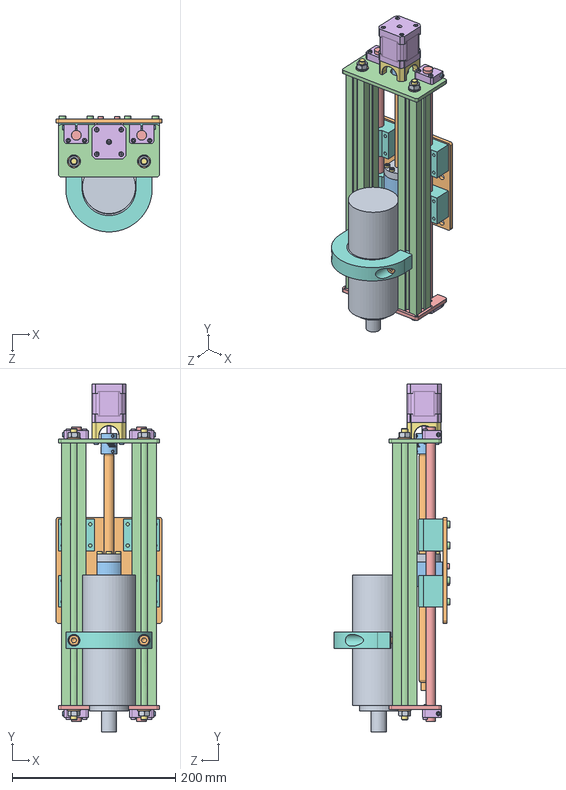
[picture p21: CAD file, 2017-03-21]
HybridCNC_v3/HybridCNC-Changed-files-only/Z axis/z axis.SLDASM
130.0 x 426.8 x 142.0 mm
ball screw nut SFU1204 fi12xfi22x40
ball screw SFU1204 fi12x300
coupler 5x8
profile aluminum 30x30x279 x 2
smooth rod fi12x314 x 2
stepper motor NEMA 17
threaded rod M8x310 x 2
Casing tipe SCE x 4
spindle
Base plate
nut mount
motor plate
Bottom plate
rod fixer x 4
adapter motor
spindle mount
DIN 934 M8 8.8 x 4
DIN 125 8.4 Grade A x 4
Torx_screw_m3-30 x 8
Torx_screw_ m5-12 x 16
Torx_screw_m4-10 x 4
Torx_screw_m3-16 x 8
Torx_screw_m4-16 x 6
nut_din_557-m8_m_6_5 x 2
Guma
screw_iso_4762-m8x35-8_8 x 2

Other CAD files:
SolidWorks_Files/Tightener Assembly.SLDASM
SolidWorks_Files/Tightener Assembly - M3.SLDASM
HybridCNC_v3/HybridCNC - 3D model/Tightener Plate - Assembly X right.SLDASM
HybridCNC_v3/HybridCNC - 3D model/Beam X - Main.SLDPRT
Drawings/Frame/Beam X - Main.SLDDRW
Drawings/Frame/Beam X1.SLDDRW
Drawings/Frame/Beam X2.SLDDRW
Drawings/Frame/Beam Y.SLDDRW
Drawings/Frame/Bracket for tighteners - left.SLDDRW
Drawings/Frame/Bracket for tighteners - right.SLDDRW
Drawings/Frame/DXF/Beam X1.DXF
Drawings/Frame/DXF/Beam X2.DXF
Drawings/Frame/DXF/Beam Y.DXF
Drawings/Frame/DXF/Bracket for tighteners - left.DXF
Drawings/Frame/DXF/Bracket for tighteners - right.DXF
Drawings/Frame/DXF/L Profile - Chain Support.DXF
Drawings/Frame/DXF/Tightener - Spacer.DXF
Drawings/Frame/DXF/Tightener - left.DXF
Drawings/Frame/DXF/Tightener - right.DXF
Drawings/Frame/L Profile - Chain Support.SLDDRW
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

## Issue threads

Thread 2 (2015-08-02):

electronics control BOM

wordsforthewise, 2015-08-02:
Hey, I'm working with Open Source Ecology (Factor E Farms out of Missouri, USA), and we're trying to get one of these operational by 13 days from now.  I'm taking care of documenting the build and getting a full BOM including control electronics.  Marcin said you guys may be releasing an update concerning that soon?  If you're not releasing it, would you mind sending me what you have so far?
Thanks,
Nate G

SloMusti, 2015-08-02:
Hi,

please get back to me in a few days, we are in full swing running
Battlemesh event here. We are working on a release that should be
completed in that timeframe.

Kind regards,
Musti

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

wordsforthewise, 2015-08-03:
Ok, thanks!

wordsforthewise, 2015-08-15:
Hey how'd the battlemesh go?  I think there is already a CNC plasma cutter here, so maybe it isn't so urgent to get the electronics plans.  It would still be nice to have them though, as I'll be on site at OSE for the next 9 days, and Marcin and I could work on it at night.  My email is the same as my github username but at gmail, if you would like to continue conversating there instead of this thread.
bless up,
Nate

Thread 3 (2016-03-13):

firmware for plasma printer

mkeyno, 2016-03-13:
hi
thanks for sharing the drawing , but I was wondering what is current cnc software status ? have you decide which platform should be developed? if so I suggested to use Marlin 3d printer firmware which is modified by[ cool guys ](https://github.com/HakanBastedt/Marlin4Due/tree/Laser)for using in laser CNC ,but I think  with some extra modification could be easily adapted for plasma cutter
my best regards

SloMusti, 2016-03-14:
We use http://goodenoughcnc.eu/toslink-cnc/ as the basis for control, the controller used can be either Arduino Uno with GRBL, Marlin or Planet-cnc and in fact any controller.

We will add detailed instructions on control system shortly.

dudemeister53, 2016-12-18:
Thank you very much for this project.  I have my goodenoughcnc assembled utilizing the Toslink system and a Planet CNC controller.  I was just wondering if you can publish the planet-cnc controller settings file you are currently using.  I'm specifically looking for information on stepper motor speed control settings,

Thank you!

SloMusti, 2016-12-27:
Settings available here: https://github.com/IRNAS/GoodEnoughCNC-PlasmaCutter/blob/master/goodenoughcnc-hybrid-planetcnc.setting

Closed 2016-12-27.

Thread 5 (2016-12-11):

Bearing Plate Hole Locations and Sizes

Steve99and04, 2016-12-11:
There is nothing that details the location / sizes of the holes and slots on the bearing plate.

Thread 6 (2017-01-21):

the plans pdf and STEP sets are incomplete

alexbodn, 2017-01-21:
hello friends,

and a big thank for the challenge to build and further study such interesting machines.
my computer runs linux with freecad, so my build will rely entirely on the STEP exports and pdf drawings.
however, these sets are not entirely covering the frame parts, and part of the solidworks have not been exported:
GoodEnoughCNC-PlasmaCutter/STEP/Nut DIN 934 M8.STEP does not exist!. skipping ...
GoodEnoughCNC-PlasmaCutter/STEP/Tightener - Outer.STEP does not exist!. skipping ...
GoodEnoughCNC-PlasmaCutter/STEP/Tightener Assembly - M1.STEP does not exist!. skipping ...
GoodEnoughCNC-PlasmaCutter/STEP/Tightener Assembly.STEP does not exist!. skipping ...
GoodEnoughCNC-PlasmaCutter/STEP/Tightener Assembly - M2.STEP does not exist!. skipping ...
GoodEnoughCNC-PlasmaCutter/STEP/Tightener Assembly - M3.STEP does not exist!. skipping ...

i also see no plan for the y beams.

p.s. could i, after building the mechanical part, order the electronic part from you?

thanks in advance,
alex

anjala, 2017-01-24:
Hi Alex,

Thank you for you message. My colleague has checked .step file: GoodEnoughCNC-PlasmaCutter-master\STEP\Plasma Beta.STEP from Github repository in Solidworks 2016 and did not find any errors or missing files. As you can see in attached picture all Tightener sub-assembly files are included.
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

I’ve uploaded a pdf drawing of Beam Y to GoodEnoughCNC-PlasmaCutter/tree/master/Drawings/Frame/PDF, you can find .dxf file of Beam Y in GoodEnoughCNC-PlasmaCutter-master\Drawings\Frame\DXF.

The assembly instructions for this machine are available here: https://goodenoughcnc-hybrid-cnc.readme.io/docs.

We offer this machine in [kit version](http://fabrikor.eu/goodenoughcnc-hybrid/goodenoughcnc-hybrid-suitcase-kit) only. (Please note that we’re currently upgrading the design of this machine - the new version will be available in April 2017.) The [ToslinkCNC](http://fabrikor.eu/electronics) can be bought separately.

Hope this answers all your questions. Let me know if you need anything else.
Best,
Anja

anjala, 2017-01-24:
Hi Alex,

Thank you for you message. My colleague has checked .step file: GoodEnoughCNC-PlasmaCutter-master\STEP\Plasma Beta.STEP from Github repository in Solidworks 2016 and did not find any errors or missing files. As you can see in attached picture all Tightener sub-assembly files are included.
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

I’ve uploaded a pdf drawing of Beam Y to GoodEnoughCNC-PlasmaCutter/tree/master/Drawings/Frame/PDF, you can find .dxf file of Beam Y in GoodEnoughCNC-PlasmaCutter-master\Drawings\Frame\DXF.

The assembly instructions for this machine are available here: https://goodenoughcnc-hybrid-cnc.readme.io/docs.

We offer this machine in [kit version](http://fabrikor.eu/goodenoughcnc-hybrid/goodenoughcnc-hybrid-suitcase-kit) only. (Please note that we’re currently upgrading the design of this machine - the new version will be available in April 2017.) The [ToslinkCNC](http://fabrikor.eu/electronics) can be bought separately.

Hope this answers all your questions. Let me know if you need anything else.
Best,
Anja

alexbodn, 2017-01-24:
thank you anja,

following your response i found that the solidworks files
Tightener Assembly* have step counter parties named Tightener 2*
however, i could find no step corresponding file for
the "Nut DIN 934 M8" solidworks file.

about the toslinkcnc 3 and 4 kits: do they contain everything electrical except the motors?

best regards,
alex

anjala, 2017-01-26:
[ToslinkCNC](http://fabrikor.eu/electronics/toslinkcnc-4-axis-kit) includes:
- 4 pcs assembled Receiver PCB's
- 1 pc assembled Transmitter PCB / Arduino shield
- 4 pcs Toslink cable 5m
Please check the full [Bill of materials](https://goodenoughcnc-hybrid-cnc.readme.io/docs/bill-of-materials) to see all the other components you'll need for the assembly.

All the documentation for GoodEnoughCNC will be revised with the new machine coming out in April 2017.

Cheers,
Anja

alexbodn, 2017-01-27:
thanks a lot anja

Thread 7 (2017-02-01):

US Standard Hose Clamp sizes for 65mm Mill Mount STL

dudemeister53, 2017-02-01:
I've attached an STL for the 65mm Mill Mount that will work with 1/2" or 9/16" size bands on US hose clamps. Please let me know if you have any questions.

[Mill Mount 65mm - Z Axis - 2 piece(s) - Standard US Hose Clamp Sizes.zip](https://github.com/IRNAS/GoodEnoughCNC-PlasmaCutter/files/743957/Mill.Mount.65mm.-.Z.Axis.-.2.piece.s.-.Standard.US.Hose.Clamp.Sizes.zip)

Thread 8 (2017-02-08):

Beams thickness

federicodecuzzi, 2017-02-08:
Hello, and first of all, thank you very much for the information given in this repository. I have a question related to Beams thickness. I am from Argentina and I have noticed that there is no 3mm thick standard steel square beam. The standard thicknesses are either 2mm or 3,2mm. ¿Is the BOM refering to 3,2mm (1/8 inch) when it says 3mm?.

Thanks.

SloMusti, 2017-02-08:
Beam thickness is not a significant parameter in the design and multiple values can work, for 100x100mm tubes (which could be of similar dimension as well) we recommend about 3mm thickness. For 40x40mm tubes (1.5x1.5in work as well) we suggest 2-3mm, you can even use aluminium ones if stainless or regular steel is not available.

federicodecuzzi, 2017-02-08:
Thank you very much. I´ll keep in touch.

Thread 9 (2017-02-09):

Linear Guide Dimensions

federicodecuzzi, 2017-02-09:
Hello again. Which should be the correct linear guide diameter and lenght?. Drawings indicate fi8X200 but the BOM says fi12X270.

SloMusti, 2017-02-09:
These are two different parts, an M8 threaded rod that is about 200mm long and the 12mm linear rod that is 270mm long. Note that lengths depend on the lengths of the Z axis you choose to make.

federicodecuzzi, 2017-02-09:
You are right, thank you again.

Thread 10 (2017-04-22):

Belt tighteners (3D printed)

federicodecuzzi, 2017-04-22:
Hello again. I was wondering if there is the possibility to replace those 3D printed parts with another type of part(I mean something more common and not 3D printed). The thing is that I find it hard to get those parts printed for me since I have no access to a 3D printer.

Thanks

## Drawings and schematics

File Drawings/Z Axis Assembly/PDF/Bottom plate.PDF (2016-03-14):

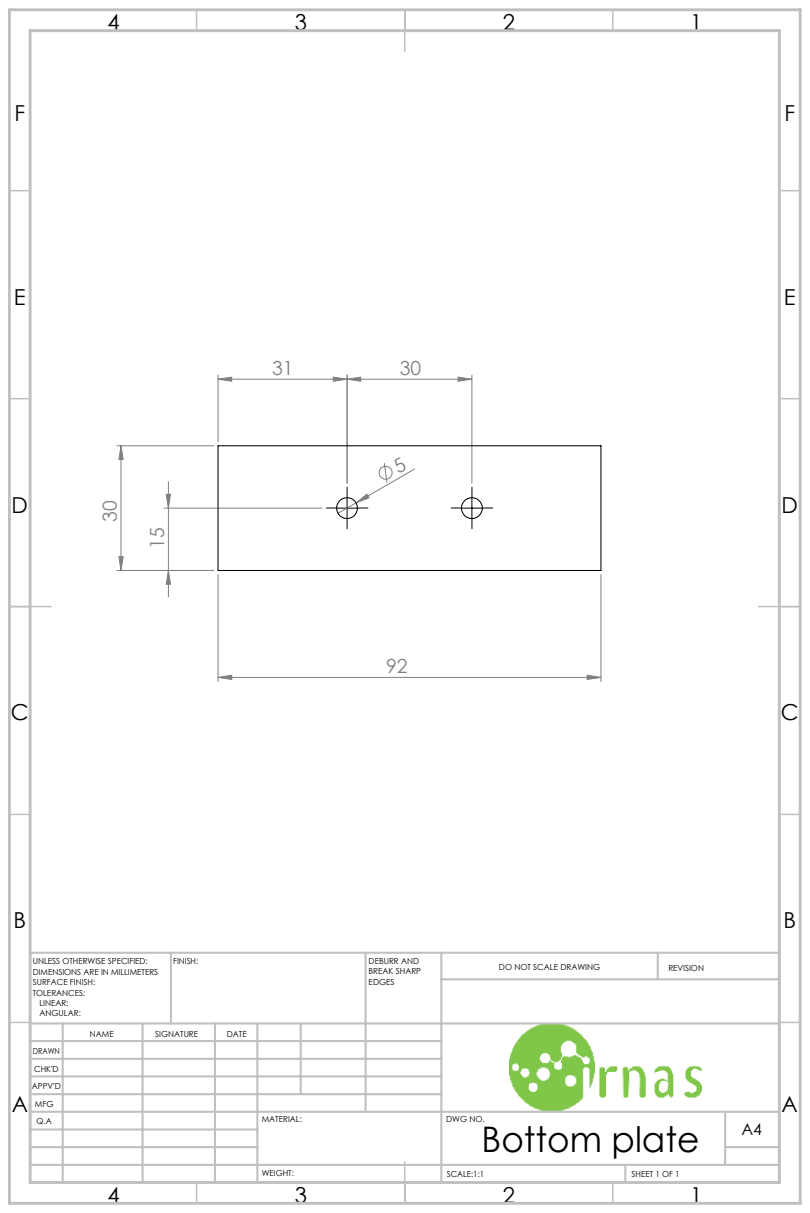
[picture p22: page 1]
FINISH:; DEBURR AND; BREAK SHARP; DO NOT SCALE DRAWING; REVISION; SCALE:1:1; SHEET 1 OF 1

UNLESS OTHERWISE SPECIFIED:
DIMENSIONS ARE IN MILLIMETERS
SURFACE FINISH:
TOLERANCES:
LINEAR:
ANGULAR:

NAME | SIGNATURE | DATE

DRAWN
CHK'D
APPV'D
MFG
Q.A | | | | MATERIAL: | DWG NO. Bottom plate | A4

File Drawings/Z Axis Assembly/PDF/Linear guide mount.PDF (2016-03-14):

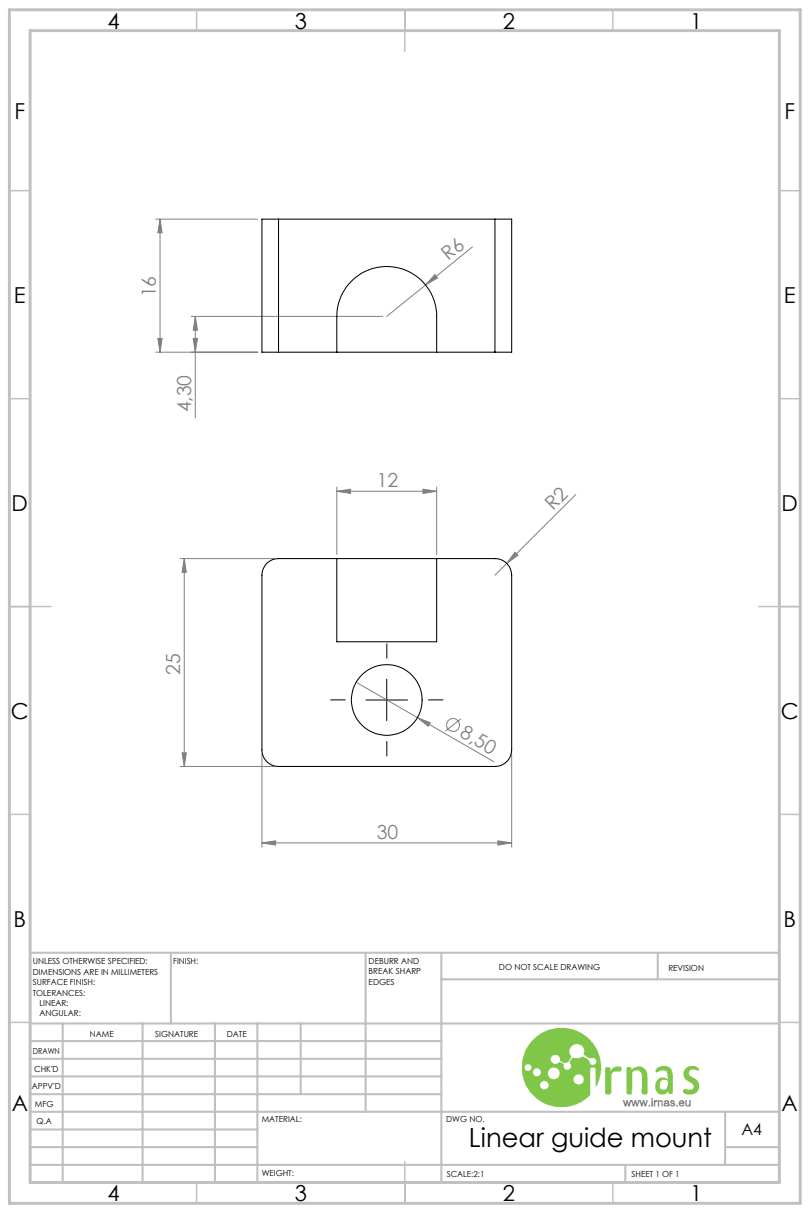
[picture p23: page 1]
FINISH:; DEBURR AND; BREAK SHARP; DO NOT SCALE DRAWING; REVISION; SCALE:2:1; SHEET 1 OF 1

UNLESS OTHERWISE SPECIFIED:
DIMENSIONS ARE IN MILLIMETERS
SURFACE FINISH:
TOLERANCES:
LINEAR:
ANGULAR:

NAME | SIGNATURE | DATE

DRAWN
CHK'D
APPV'D
MFG
Q.A | | | | MATERIAL: | DWG NO. Linear guide mount | A4

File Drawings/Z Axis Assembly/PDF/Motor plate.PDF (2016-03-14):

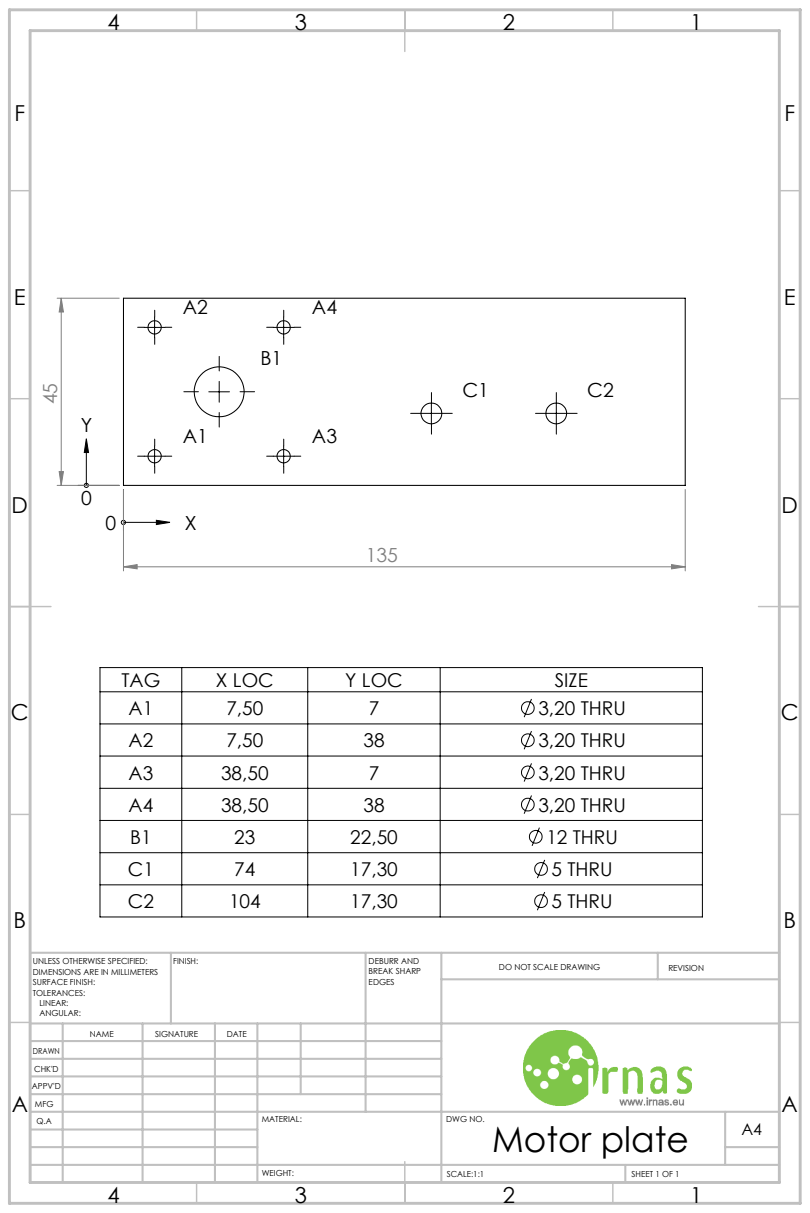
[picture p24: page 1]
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

TAG | X LOC | Y LOC | SIZE
A1 | 7,50 | 7 | 3,20 THRU
A2 | 7,50 | 38 | 3,20 THRU
A3 | 38,50 | 7 | 3,20 THRU
A4 | 38,50 | 38 | 3,20 THRU
B1 | 23 | 22,50 | 12 THRU
C1 | 74 | 17,30 | 5 THRU
C2 | 104 | 17,30 | 5 THRU

UNLESS OTHERWISE SPECIFIED:
DIMENSIONS ARE IN MILLIMETERS
SURFACE FINISH:
TOLERANCES:
LINEAR:
ANGULAR:

NAME | SIGNATURE | DATE

DRAWN
CHK'D
APPV'D
MFG
Q.A | | | | MATERIAL: | DWG NO. Motor plate | A4

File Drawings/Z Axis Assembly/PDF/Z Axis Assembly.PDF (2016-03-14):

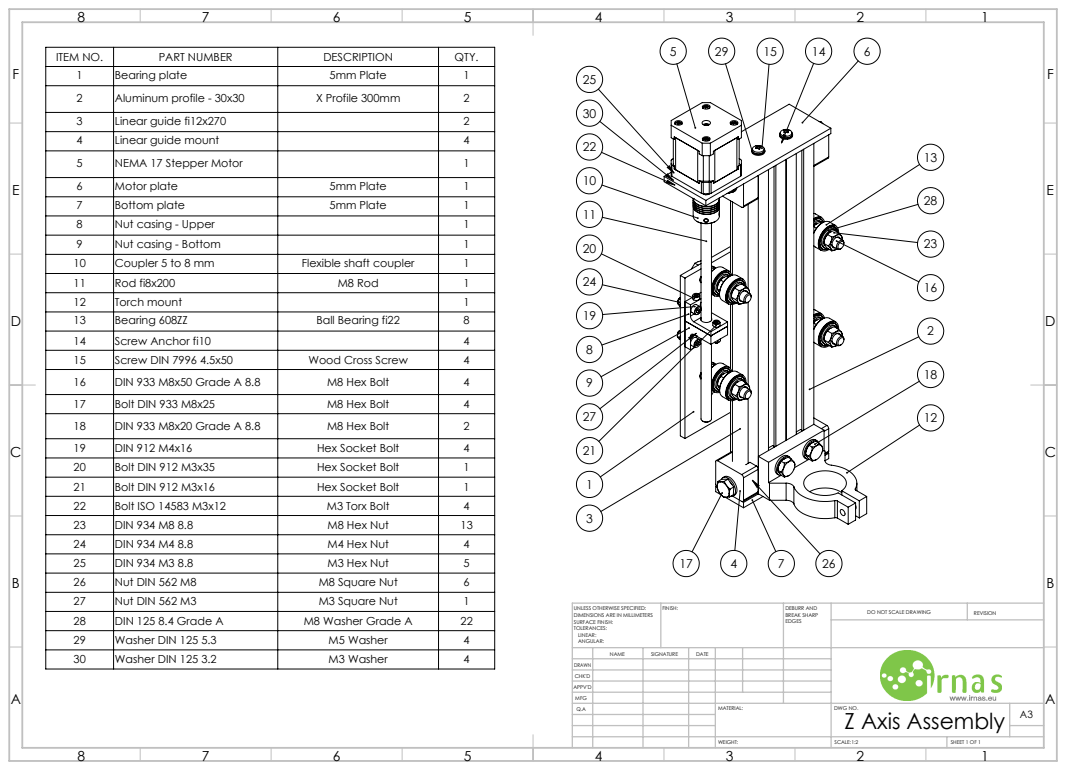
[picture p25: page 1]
DIN 934 M8 8.8; M8 Hex Nut; FINISH:; DEBURR AND; BREAK SHARP; DO NOT SCALE DRAWING; REVISION; SCALE:1:2; SHEET 1 OF 1

ITEM NO. | PART NUMBER | DESCRIPTION | QTY.
1 | Bearing plate | 5mm Plate | 1
2 | Aluminum profile - 30x30 | X Profile 300mm | 2
3 | Linear guide fi12x270 | | 2
4 | Linear guide mount | | 4
5 | NEMA 17 Stepper Motor | | 1
6 | Motor plate | 5mm Plate | 1
7 | Bottom plate | 5mm Plate | 1
8 | Nut casing - Upper | | 1
9 | Nut casing - Bottom | | 1
10 | Coupler 5 to 8 mm | Flexible shaft coupler | 1
11 | Rod fi8x200 | M8 Rod | 1
12 | Torch mount | | 1
13 | Bearing 608ZZ | Ball Bearing fi22 | 8
14 | Screw Anchor fi10 | | 4
15 | Screw DIN 7996 4.5x50 | Wood Cross Screw | 4
16 | DIN 933 M8x50 Grade A 8.8 | M8 Hex Bolt | 4
17 | Bolt DIN 933 M8x25 | M8 Hex Bolt | 4
18 | DIN 933 M8x20 Grade A 8.8 | M8 Hex Bolt | 2
19 | DIN 912 M4x16 | Hex Socket Bolt | 4
20 | Bolt DIN 912 M3x35 | Hex Socket Bolt | 1
21 | Bolt DIN 912 M3x16 | Hex Socket Bolt | 1
22 | Bolt ISO 14583 M3x12 | M3 Torx Bolt | 4

24 | DIN 934 M4 8.8 | M4 Hex Nut | 4
25 | DIN 934 M3 8.8 | M3 Hex Nut | 5
26 | Nut DIN 562 M8 | M8 Square Nut | 6
27 | Nut DIN 562 M3 | M3 Square Nut | 1
28 | DIN 125 8.4 Grade A | M8 Washer Grade A | 22
29 | Washer DIN 125 5.3 | M5 Washer | 4
DRAWN | NAME | SIGNATURE | DATE
30 | Washer DIN 125 3.2 | M3 Washer | 4

UNLESS OTHERWISE SPECIFIED:
DIMENSIONS ARE IN MILLIMETERS
SURFACE FINISH:
TOLERANCES:
LINEAR:
ANGULAR:

CHK'D
APPV'D
MFG
Q.A | MATERIAL: | DWG NO. Z Axis Assembly | A3

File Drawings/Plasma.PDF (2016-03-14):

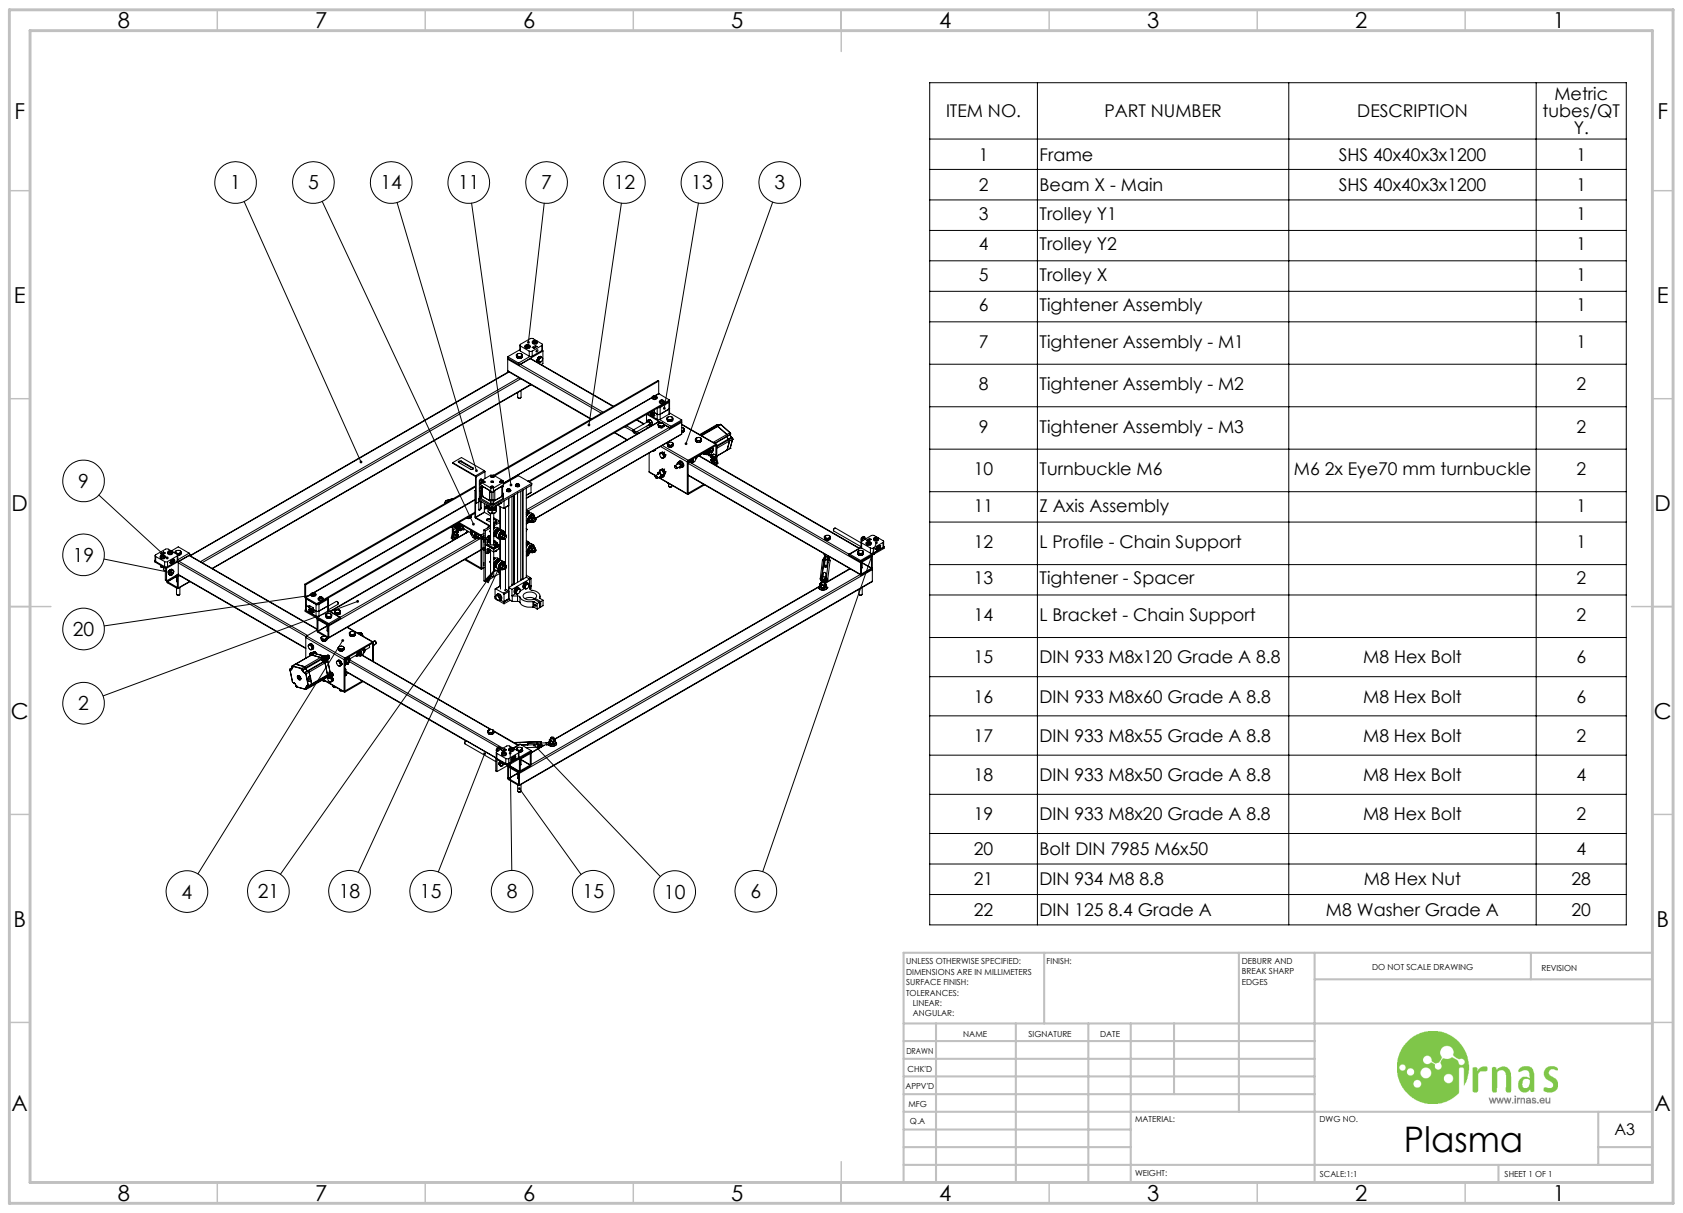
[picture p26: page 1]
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

ITEM NO. | PART NUMBER | DESCRIPTION | Metric tubes/QT Y.

1 | Frame | SHS 40x40x3x1200 | 1
2 | Beam X - Main | SHS 40x40x3x1200 | 1
3 | Trolley Y1 | | 1
4 | Trolley Y2 | | 1
5 | Trolley X | | 1
6 | Tightener Assembly | | 1
7 | Tightener Assembly - M1 | | 1
8 | Tightener Assembly - M2 | | 2
9 | Tightener Assembly - M3 | | 2
10 | Turnbuckle M6 | M6 2x Eye70 mm turnbuckle | 2
11 | Z Axis Assembly | | 1
12 | L Profile - Chain Support | | 1
13 | Tightener - Spacer | | 2
14 | L Bracket - Chain Support | | 2
15 | DIN 933 M8x120 Grade A 8.8 | M8 Hex Bolt | 6
16 | DIN 933 M8x60 Grade A 8.8 | M8 Hex Bolt | 6
17 | DIN 933 M8x55 Grade A 8.8 | M8 Hex Bolt | 2
18 | DIN 933 M8x50 Grade A 8.8 | M8 Hex Bolt | 4
19 | DIN 933 M8x20 Grade A 8.8 | M8 Hex Bolt | 2
20 | Bolt DIN 7985 M6x50 | | 4
21 | DIN 934 M8 8.8 | M8 Hex Nut | 28
22 | DIN 125 8.4 Grade A | M8 Washer Grade A | 20

UNLESS OTHERWISE SPECIFIED:
DIMENSIONS ARE IN MILLIMETERS
SURFACE FINISH:
TOLERANCES:
LINEAR:
ANGULAR:

NAME | SIGNATURE | DATE

DRAWN
CHK'D
APPV'D
MFG
Q.A | | | | MATERIAL: | DWG NO. Plasma | A3

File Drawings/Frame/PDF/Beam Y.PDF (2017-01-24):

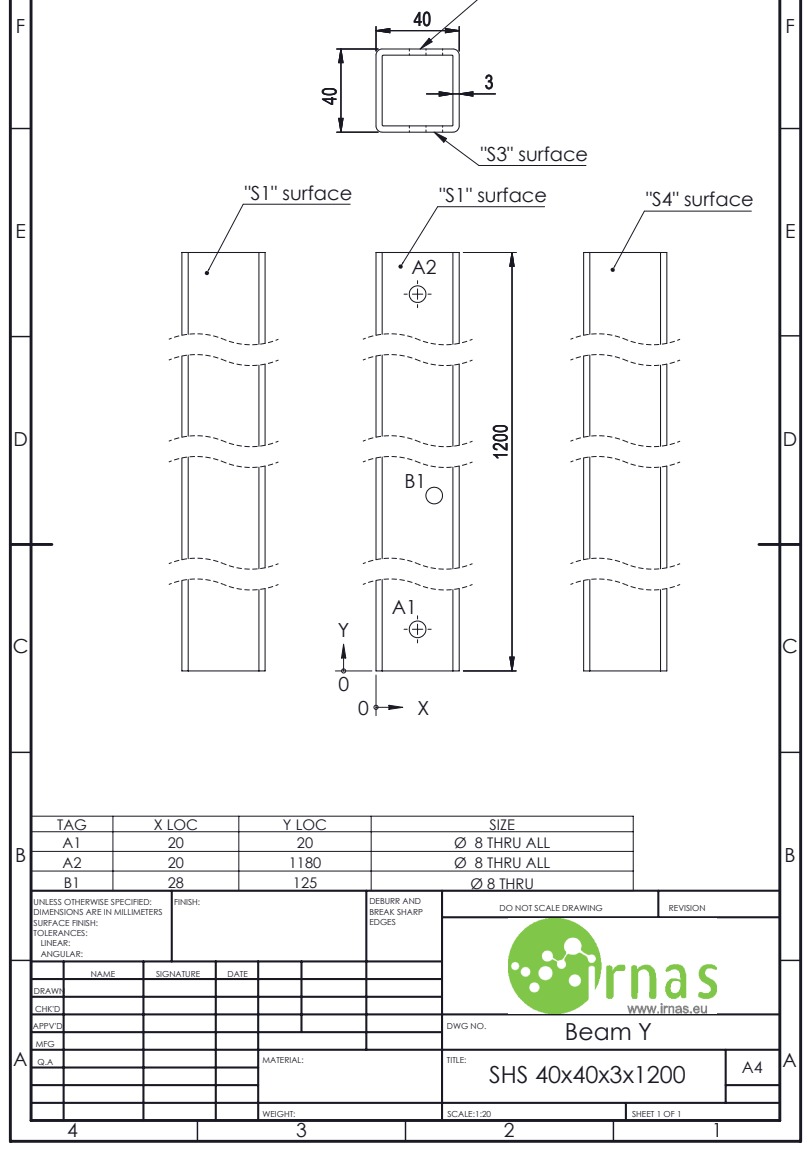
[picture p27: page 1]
"S1" surface; "S3" surface "S4" surface "S1" surface; SCALE:1:20; SHEET 1 OF 1

TAG | X LOC | Y LOC | SIZE
A1 | 20 | 20 | Ø 8 THRU ALL
A2 | 20 | 1180 | Ø 8 THRU ALL
B1 | 28 | 125 | Ø 8 THRU

UNLESS OTHERWISE SPECIFIED: DIMENSIONS ARE IN MILLIMETERS SURFACE FINISH: TOLERANCES: LINEAR: ANGULAR: | FINISH: | DEBURR AND BREAK SHARP EDGES | DO NOT SCALE DRAWING | REVISION

NAME | SIGNATURE | DATE

DRAWN
CHK'D
APPV'D | | | | | | | Beam Y DWG NO.

MFG
Q.A | | | | MATERIAL: | TITLE: SHS 40x40x3x1200 | A4

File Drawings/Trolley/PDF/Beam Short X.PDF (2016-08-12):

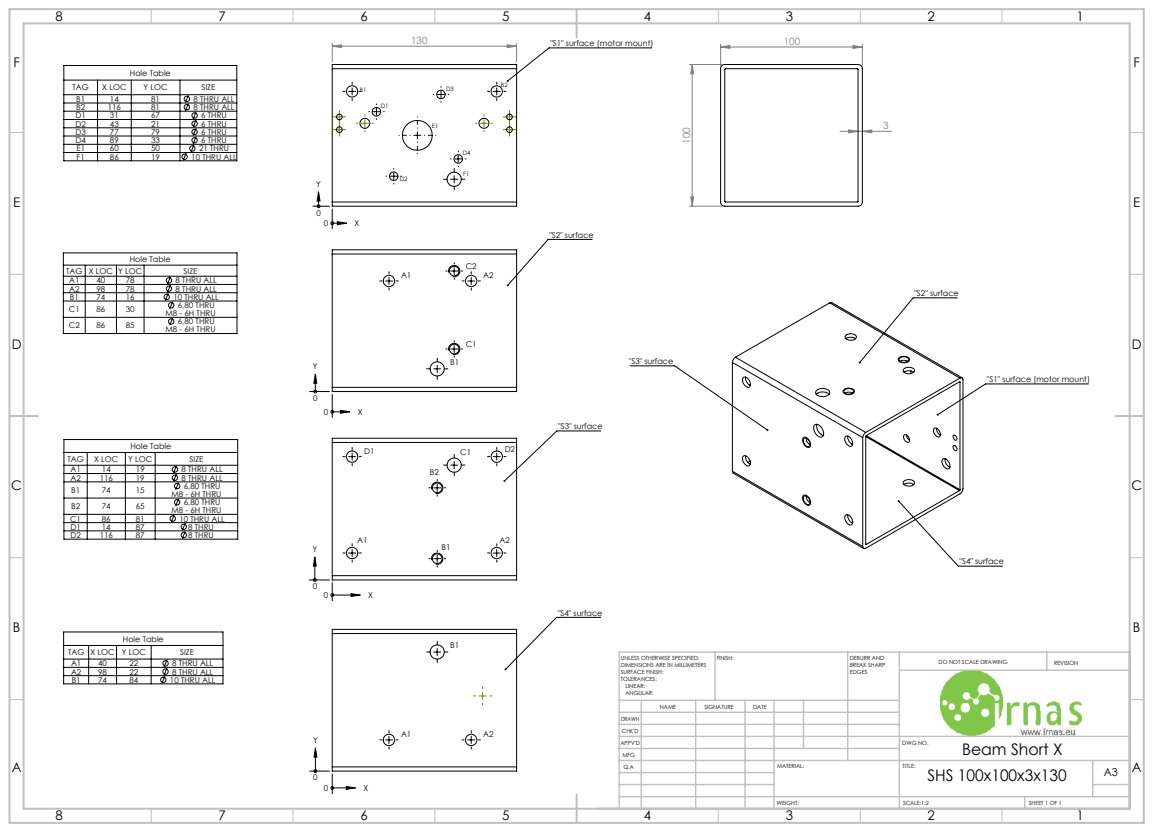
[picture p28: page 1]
"S1" surface (motor mount); "S2" surface; "S3" surface; "S4" surface; Hole Table; SCALE:1:2; SHEET 1 OF 1

TAG | X LOC | Y LOC | SIZE
B1 | 14 | 81 | 8 THRU ALL
B2 | 116 | 81 | 8 THRU ALL
D1 | 31 | 67 | 6 THRU
D2 | 43 | 21 | 6 THRU
D3 | 77 | 79 | 6 THRU
D4 | 89 | 33 | 6 THRU
E1 | 60 | 50 | 21 THRU
F1 | 86 | 19 | 10 THRU ALL

A1 | 40 | 78 | 8 THRU ALL
A2 | 98 | 78 | 8 THRU ALL
B1 | 74 | 16 | 10 THRU ALL
C1 | 86 | 30 | 6,80 THRU M8 - 6H THRU
C2 | 86 | 85 | 6,80 THRU M8 - 6H THRU

"S1" surface (motor mount)

A1 | 14 | 19 | 8 THRU ALL
A2 | 116 | 19 | 8 THRU ALL
B1 | 74 | 15 | 6,80 THRU M8 - 6H THRU
B2 | 74 | 65 | 6,80 THRU M8 - 6H THRU
C1 | 86 | 81 | 10 THRU ALL
D1 | 14 | 87 | 8 THRU
D2 | 116 | 87 | 8 THRU

A1 | 40 | 22 | 8 THRU ALL
A2 | 98 | 22 | 8 THRU ALL
B1 | 74 | 84 | 10 THRU ALL

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

NAME | SIGNATURE | DATE

DRAWN
CHK'D
APPV'D | | | | | | | DWG NO. Beam Short X
MFG
Q.A | | | | MATERIAL: | TITLE: SHS 100x100x3x130 | A3

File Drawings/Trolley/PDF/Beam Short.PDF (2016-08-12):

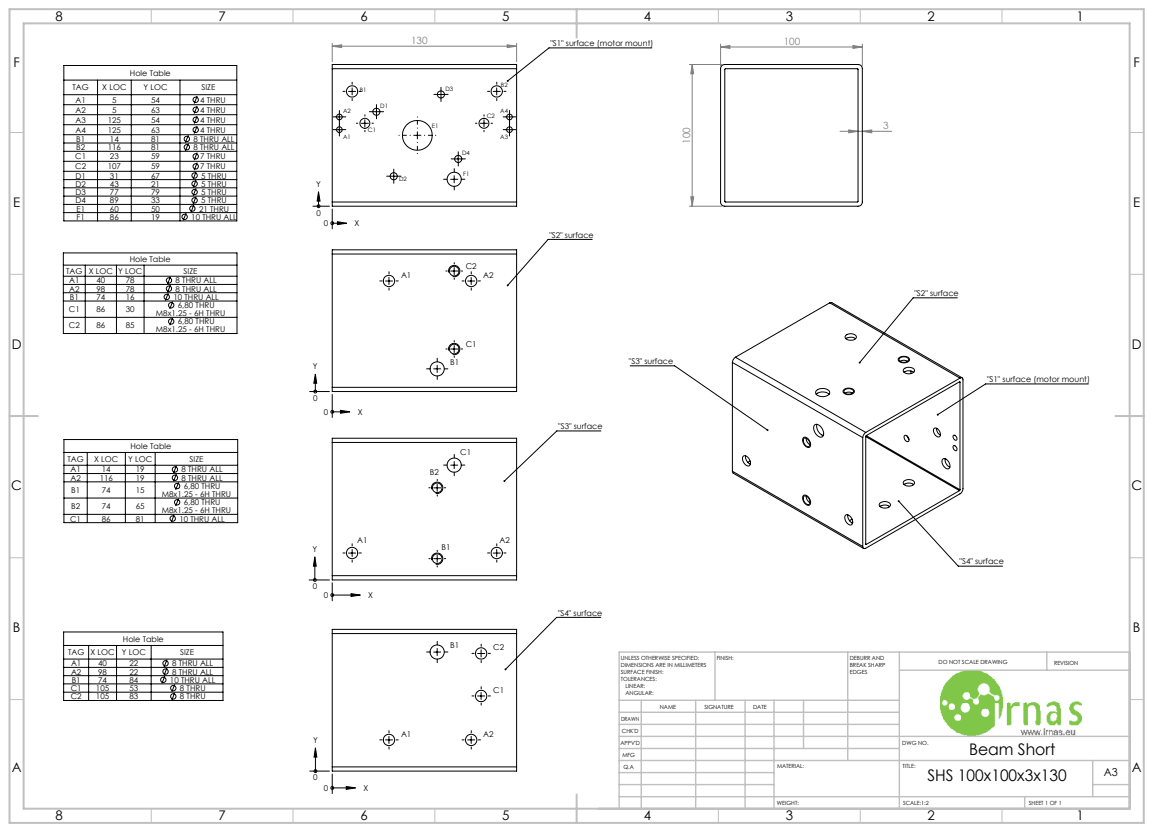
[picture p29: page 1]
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

TAG | X LOC | Y LOC | SIZE
A1 | 5 | 54 | 4 THRU
A2 | 5 | 63 | 4 THRU
A3 | 125 | 54 | 4 THRU
A4 | 125 | 63 | 4 THRU
B1 | 14 | 81 | 8 THRU ALL
B2 | 116 | 81 | 8 THRU ALL
C1 | 23 | 59 | 7 THRU
C2 | 107 | 59 | 7 THRU
D1 | 31 | 67 | 5 THRU
D2 | 43 | 21 | 5 THRU
D3 | 77 | 79 | 5 THRU
D4 | 89 | 33 | 5 THRU
E1 | 60 | 50 | 21 THRU
F1 | 86 | 19 | 10 THRU ALL

A1 | 40 | 78 | 8 THRU ALL
A2 | 98 | 78 | 8 THRU ALL
B1 | 74 | 16 | 10 THRU ALL
C1 | 86 | 30 | 6,80 THRU M8x1.25 - 6H THRU
C2 | 86 | 85 | 6,80 THRU M8x1.25 - 6H THRU

"S1" surface (motor mount)

A1 | 14 | 19 | 8 THRU ALL
A2 | 116 | 19 | 8 THRU ALL
B1 | 74 | 15 | 6,80 THRU M8x1.25 - 6H THRU
B2 | 74 | 65 | 6,80 THRU M8x1.25 - 6H THRU
C1 | 86 | 81 | 10 THRU ALL

A1 | 40 | 22 | 8 THRU ALL
A2 | 98 | 22 | 8 THRU ALL
B1 | 74 | 84 | 10 THRU ALL
C1 | 105 | 53 | 8 THRU
C2 | 105 | 83 | 8 THRU

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

NAME | SIGNATURE | DATE

DRAWN
CHK'D
APPV'D | | | | | | | DWG NO. Beam Short
MFG
Q.A | | | | MATERIAL: | TITLE: SHS 100x100x3x130 | A3

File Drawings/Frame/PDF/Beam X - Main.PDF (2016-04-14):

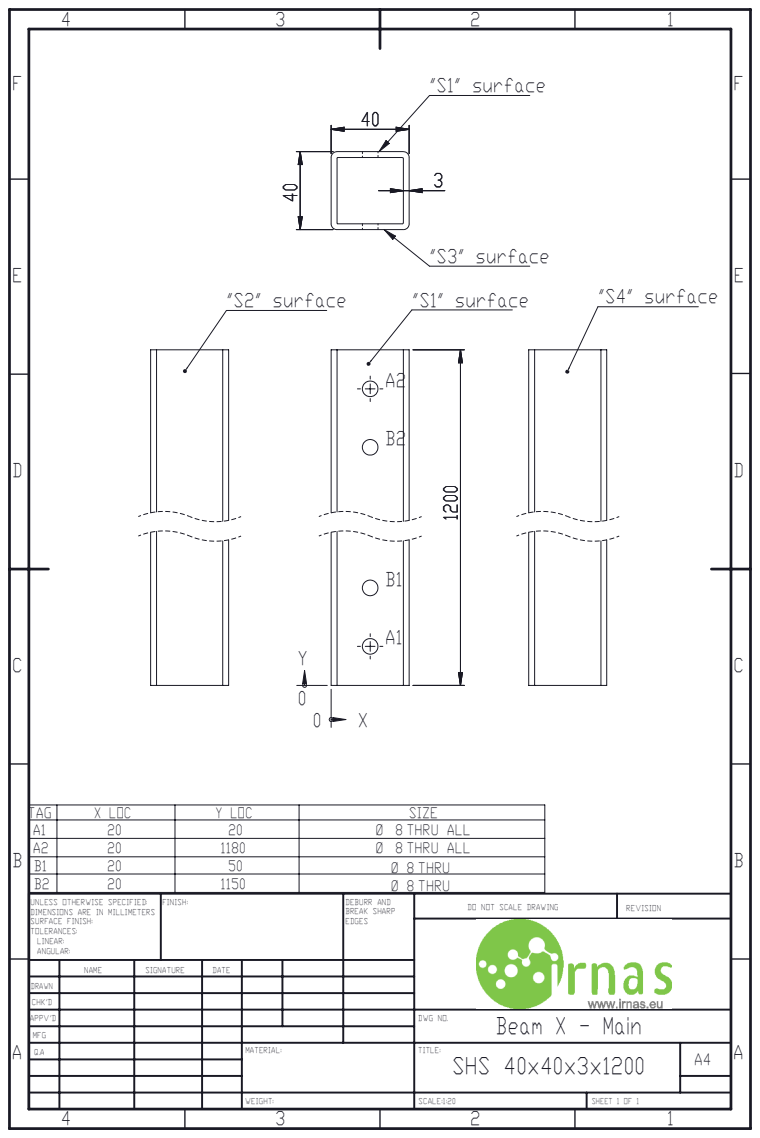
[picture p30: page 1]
"S1" surface; "S3" surface; "S2" surface; "S4" surface; SCALE:1:20; SHEET 1 OF 1

TAG | X LOC | Y LOC | SIZE
A1 | 20 | 20 | Ø 8 THRU ALL
A2 | 20 | 1180 | Ø 8 THRU ALL
B1 | 20 | 50 | Ø 8 THRU
B2 | 20 | 1150 | Ø 8 THRU

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

NAME | SIGNATURE | DATE

DRAWN
CHK'D
APPV'D | | | | | | | Beam X - Main DWG NO.
MFG
Q.A | | | | MATERIAL: | TITLE: SHS 40x40x3x1200 | A4

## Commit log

2015-06-19 Initial release
    [Flange for M8 Nut.STL, Limit switch screw mount.STL, Rod flange.STL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]
2016-01-20 BOM update
    Drawings bug fix and BOM update
    [Base plate.SLDDRW, Base plate.SLDPRT, Beam Short X.SLDDRW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]
2016-03-01 large mill update
2016-03-14 New Version Upload
    [Aluminum profile - 30x30.SLDPRT, Aluminum profile - 30x30.STEP, Base plate.DXF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]
2016-04-14 Latest Version Upload
    Small changes on trolley parts
    [Beam Short Y1.SLDPRT, Beam Short Y2.SLDPRT, Beam Short.DXF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]
2016-04-14 Latest Version Upload
    Uploaded models of trolleys without tapped holes
    [Beam Short X - Drilled Holes.SLDPRT, Beam Short X - Drilled Holes.STEP, Beam Short Y1 - Drilled Holes.SLDPRT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]
2016-05-23 Latest version
    Added STL files for 3D printing
    [Electronic Box - Plasma.STL, Electronic Box Cover - Plasma.STL, Fastener NEMA 23 Stepper Motor - Electronic Box.STL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]
2016-05-26 Stable Version
    Upload of latest version
    [Aluminum profile - 30x30.SLDPRT, Aluminum profile - 30x30.STEP, Base plate.SLDPRT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]
2016-06-13 Latest version
    Documentation corrections
    [Beam Short X - Drilled Holes.SLDPRT, Beam Short X - Drilled Holes.STEP, Beam Short X.DXF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]
2016-06-14 Latest version
    Small corrections
    [Electronic Box - Plasma - 4 piece(s).STL, Electronic Box Cover - Plasma - 4 piece(s).STL, Fastener NEMA 23 Stepper Motor - Electronic Box - 3 piece(s).STL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]
2016-06-14 Latest corrections
    Correctly oriented parts for 3D printing in STL files
    [Electronic Box - Plasma - 4 piece(s).STL, Electronic Box Cover - Plasma - 4 piece(s).STL, Linear guide mount - 4 piece(s).STL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]
2017-03-21 improvements upload
    [210217-5x16.SLDPRT, 210217-6x16.SLDPRT, Base plate.SLDPRT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]
